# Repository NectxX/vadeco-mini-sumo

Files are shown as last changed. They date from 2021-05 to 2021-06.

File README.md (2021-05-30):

# vadeco-mini-sumo
Repositório destinado à criação da placa de circuito impresso

Neste esquemático, fora realizada conexão dos sensores de linha e distância (conectores), de duas pontes H, do microstart remoto e do regulador de tensão ajustável com a plataforma Arduino.

A saber:
Para os sensores de linha, de acordo com o módulo selecionado para o projeto, há a opção de utilizar as saídas digitais ou analógicas. Fora utilizado as saídas analógicas, pois a prioridade dos pinos digitais do arduino foi destinado aos sensores de distância.

Diferenças do Gundabad para o Vadeco:
-Não foi utilizado CI's de porta NOT e AND, pois houve margem suficiente de pinos para conectar todos os dispositivos ao Arduino. Logo, toda a estratégia de funcionamento do robô viria exclusivamente do código de programação.
-O motor e o Arduino no Vadeco são alimentados pela mesma tensão de 6V oriunda do regulador LM2596. Diferentemente do Gundabad, que alimenta os motores diretamente com a tensão da bateria.

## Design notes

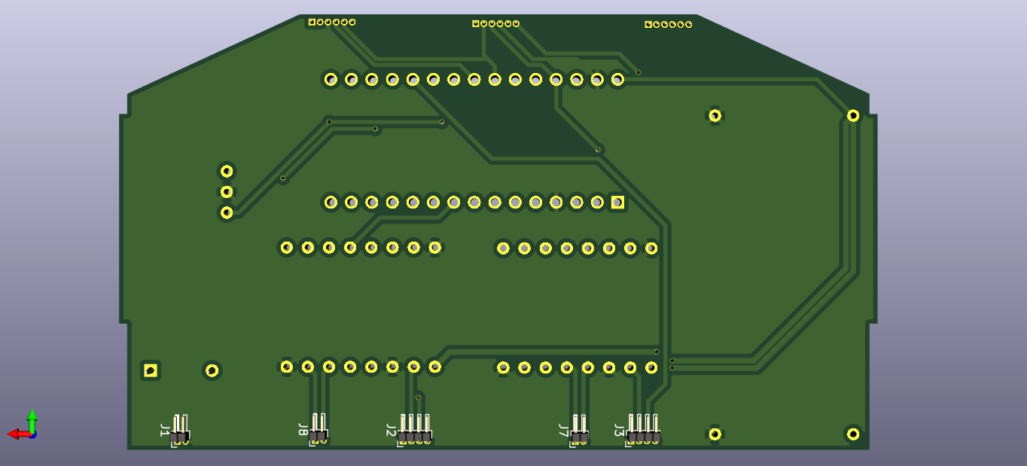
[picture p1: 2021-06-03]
Vadeco-PCB/Vadeco-PCB_Back.png

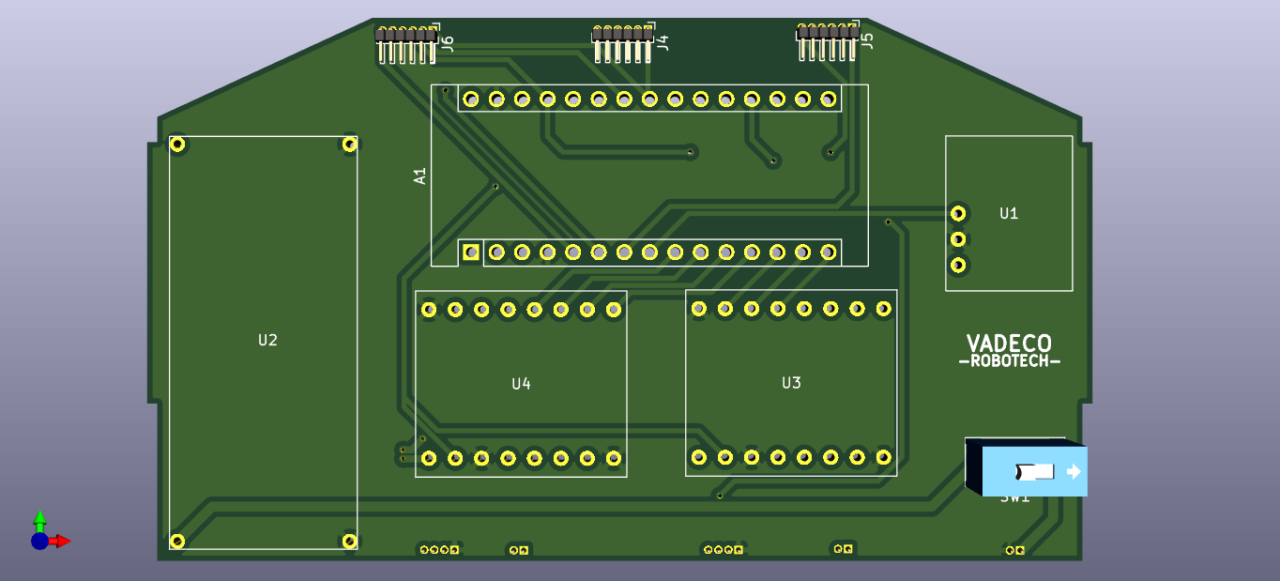
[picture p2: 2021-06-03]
Vadeco-PCB/Vadeco-PCB_Front.png

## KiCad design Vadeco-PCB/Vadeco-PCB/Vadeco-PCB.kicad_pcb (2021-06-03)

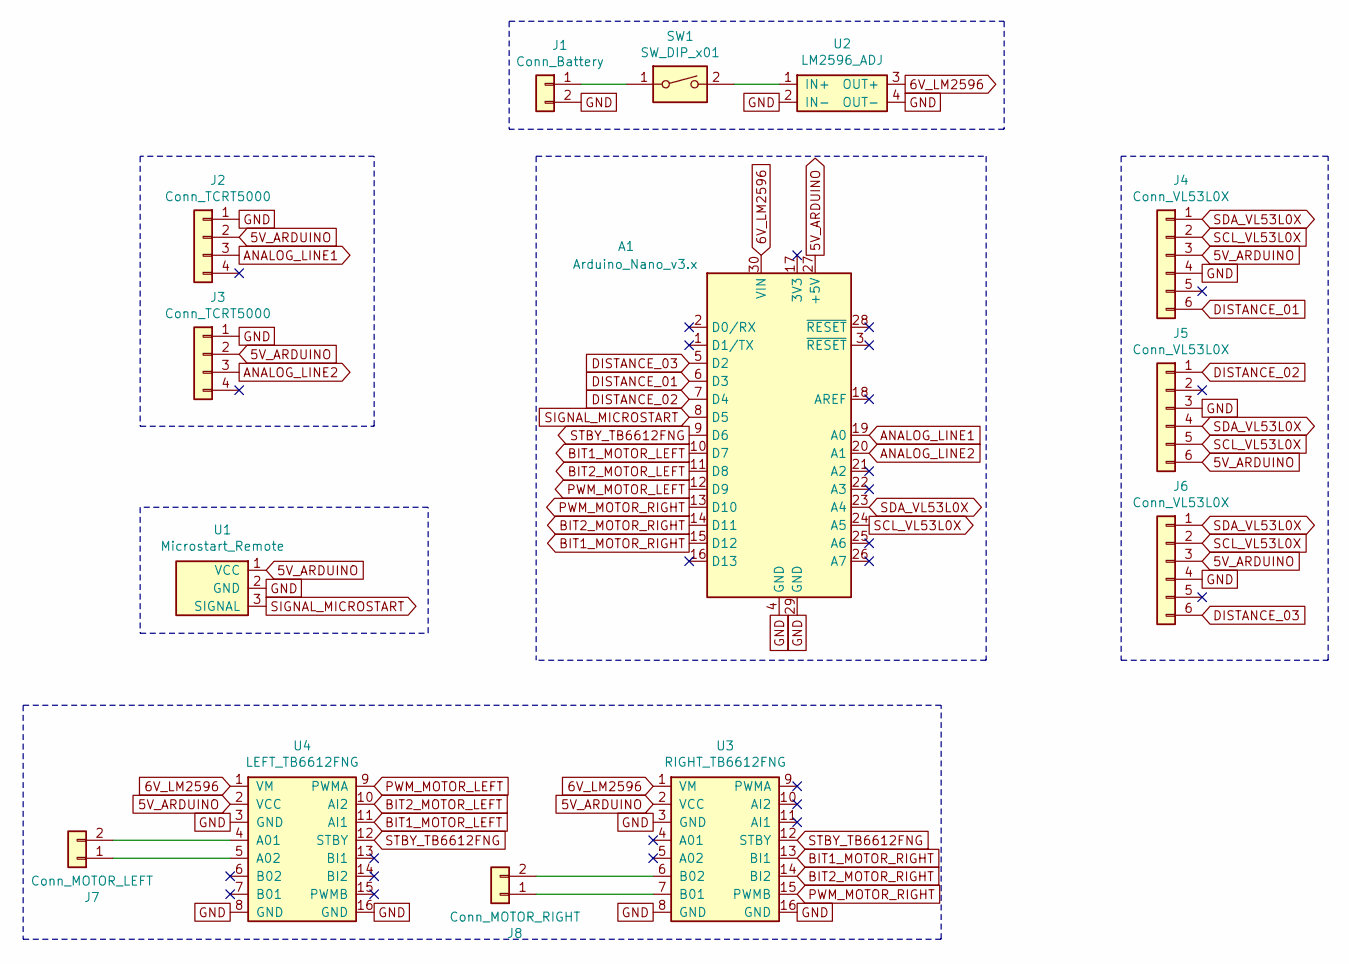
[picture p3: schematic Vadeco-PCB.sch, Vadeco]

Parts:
A1: Arduino_Nano_v3.x; Arduino_Nano
J1: Conn_Battery; PinHeader_1x02_P1.00mm_Horizontal
J2, J3: Conn_TCRT5000; PinHeader_1x04_P1.00mm_Horizontal
J4, J5, J6: Conn_VL53L0X; PinHeader_1x06_P1.00mm_Horizontal
J7: Conn_MOTOR_LEFT; PinHeader_1x02_P1.00mm_Horizontal
J8: Conn_MOTOR_RIGHT; PinHeader_1x02_P1.00mm_Horizontal
SW1: SW_DIP_x01; SW_DIP_SPSTx01_Slide_9.78x4.72mm_W7.62mm_P2.54mm
U1: Microstart_Remote; MICROSTART_MODULE
U2: LM2596_ADJ
U3: RIGHT_TB6612FNG; TB6612FNG
U4: LEFT_TB6612FNG; TB6612FNG

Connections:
5V_ARDUINO: A1.27 (+5V), J2.2, J3.2, J4.3, J5.6, J6.3, U1.1 (VCC), U3.2 (VCC), U4.2 (VCC)
6V_LM2596: A1.30 (VIN), U2.3 (OUT+), U3.1 (VM), U4.1 (VM)
ANALOG_LINE1: A1.19 (A0), J2.3
ANALOG_LINE2: A1.20 (A1), J3.3
BIT1_MOTOR_LEFT: A1.10 (D7), U4.11 (AI1)
BIT1_MOTOR_RIGHT: A1.15 (D12), U3.13 (BI1)
BIT2_MOTOR_LEFT: A1.11 (D8), U4.10 (AI2)
BIT2_MOTOR_RIGHT: A1.14 (D11), U3.14 (BI2)
DISTANCE_01: A1.6 (D3), J4.6
DISTANCE_02: A1.7 (D4), J5.1
DISTANCE_03: A1.5 (D2), J6.6
GND: A1.4 (GND), A1.29 (GND), J1.2, J2.1, J3.1, J4.4, J5.3, J6.4, U1.2 (GND), U2.2 (IN-), U2.4 (OUT-), U3.3 (GND), U3.8 (GND), U3.16 (GND), U4.3 (GND), U4.8 (GND), U4.16 (GND)
unnamed: J1.1, SW1.1
unnamed: J7.1, U4.5 (A02)
unnamed: J7.2, U4.4 (A01)
unnamed: J8.1, U3.7 (B01)
unnamed: J8.2, U3.6 (B02)
unnamed: SW1.2, U2.1 (IN+)
PWM_MOTOR_LEFT: A1.12 (D9), U4.9 (PWMA)
PWM_MOTOR_RIGHT: A1.13 (D10), U3.15 (PWMB)
SCL_VL53L0X: A1.24 (A5), J4.2, J5.5, J6.2
SDA_VL53L0X: A1.23 (A4), J4.1, J5.4, J6.1
SIGNAL_MICROSTART: A1.8 (D5), U1.3 (SIGNAL)
STBY_TB6612FNG: A1.9 (D6), U3.12 (STBY), U4.12 (STBY)

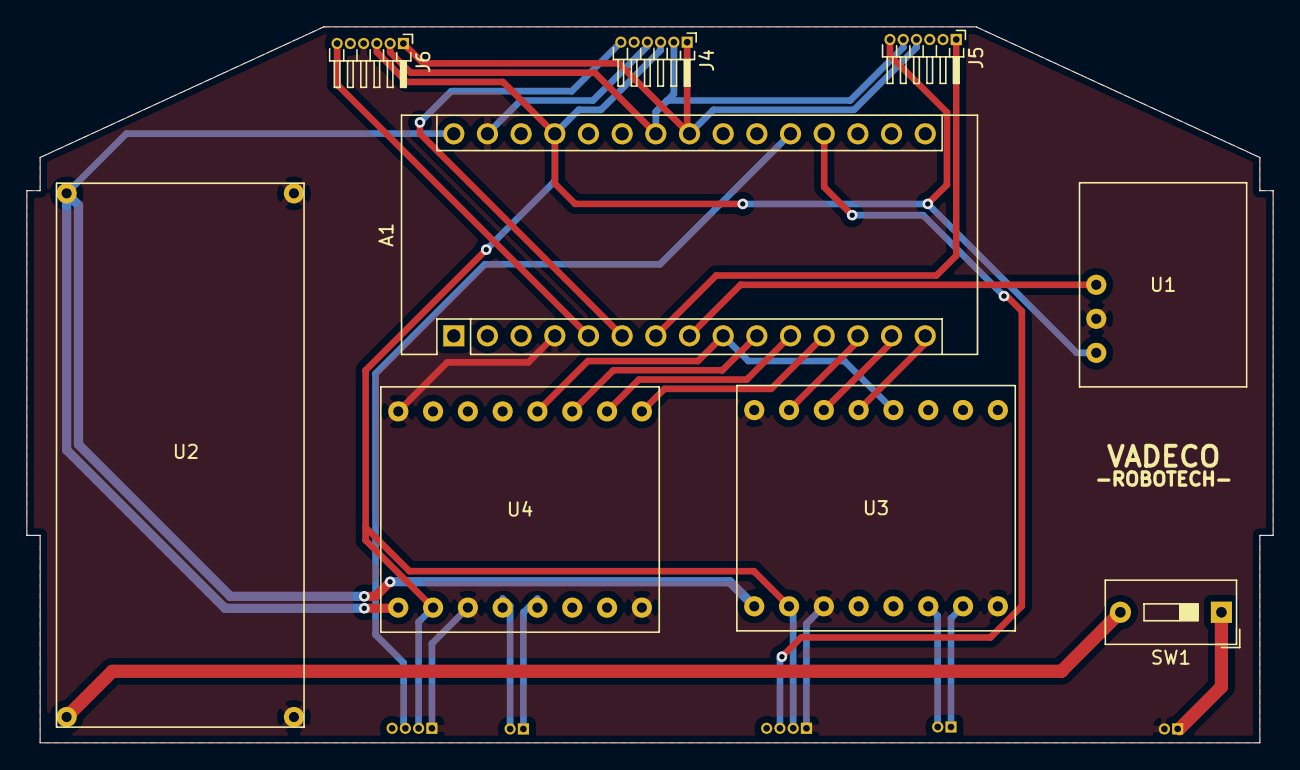
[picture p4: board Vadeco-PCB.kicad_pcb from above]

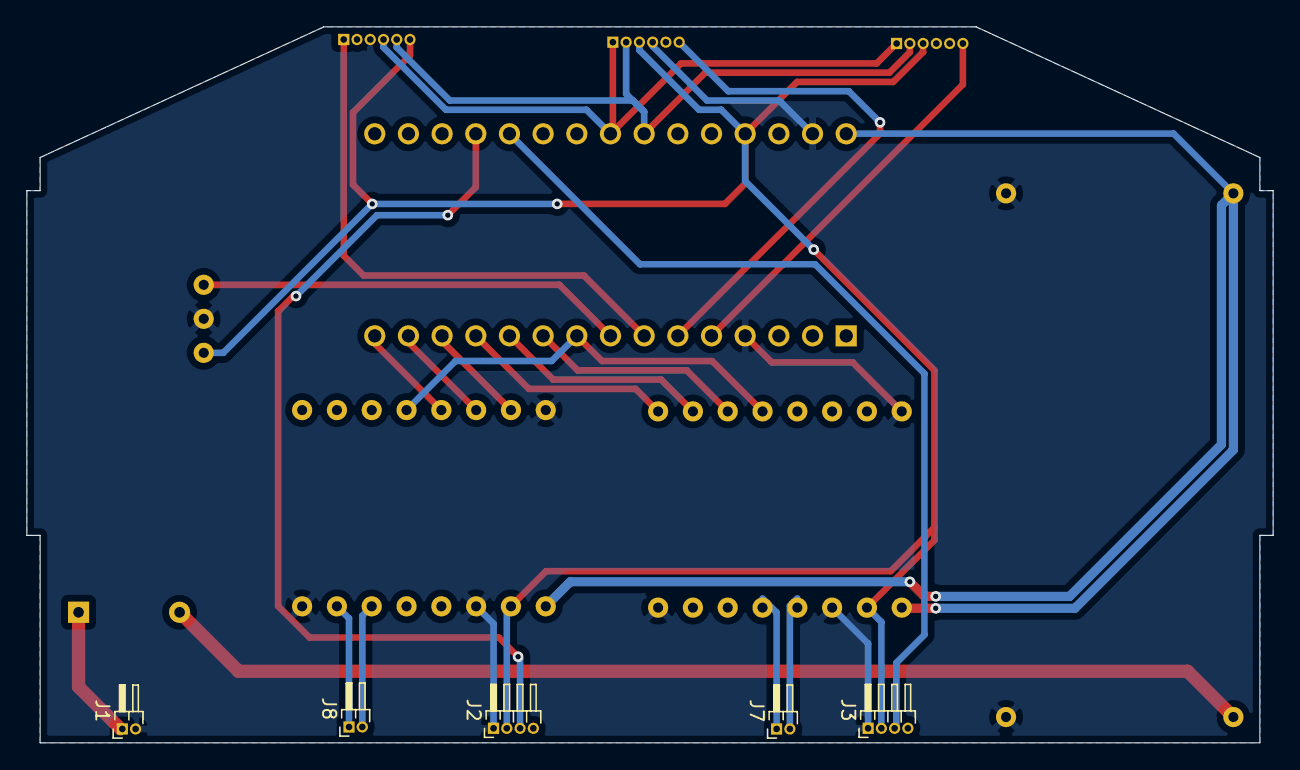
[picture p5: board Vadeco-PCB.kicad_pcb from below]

Board: 2 copper layers, 94.0 x 54.0 mm, 14 parts (5 on the bottom side), 24 nets.

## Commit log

2021-05-30 schematic without arduino connection and h bridge
    [Vadeco-PCB.kicad_pcb, Vadeco-PCB.sch]
2021-05-30 schematic done
    [Vadeco-PCB.sch]
2021-05-30 associating footprint lm2596
    [Vadeco-PCB.sch]
2021-05-31 microstart and tb6612fng footprints
    [Vadeco-PCB.sch]
2021-05-31 all footprints associated and placed to PCB
    [Vadeco-PCB.kicad_pcb, Vadeco-PCB.sch]
2021-06-01 final project v1
    [Vadeco-PCB.kicad_pcb]
2021-06-01 generating topside and backside view
    [Vadeco-PCB.kicad_pcb]
2021-06-03 schematic v3 and PCB v2
    [Vadeco-PCB.kicad_pcb, Vadeco-PCB.sch]
